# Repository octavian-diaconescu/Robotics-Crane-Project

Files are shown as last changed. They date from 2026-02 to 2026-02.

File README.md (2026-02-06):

# Robotics Crane Project

## Description
The crane can rotate 180° and raise or lower a hook to pick up and place objects anywhere within its operating area. The project prioritizes lightweight construction and simplicity, making it suitable for learning mechanical design, motion control, and basic automation using mostly 3D-printed parts. It is intended as a hands-on platform for experimenting with real-world robotic concepts such as load handling, stability, and coordinated multi-axis movement at a small scale.

## Required Components
- [x] 4 x **Stepper Motors** for controlling each moving part
- [x] 4 x **ULN2003 Motor Drivers**
- [x] **Bluetooth Controller** (e.g., PS4, Xbox, or generic Bluetooth gamepad)
- [x] **ESP32** Board
- [x] 2 x **Breadboard Mini**
- [x] 1 x **Medium Breadboard**
- [x] **Wires/Jumpers** as needed 
- [x] 16 x AA **Alkaline Batteries**
- [x] High tension, low diameter **nylon**(the fishing kind)
- [x] **Lead weights** for creating tension in the hook

## Initial Questions

### 1. What is the system boundary?
The system consists of the crane structure, the ESP32 control board, the breadboard-mounted electronic components (motor drivers), and the motors responsible for rotation, trolley movement, and hook lifting. These components are integrated into the crane assembly, with electronics housed in a 3D-printed enclosure and wiring routed beneath the base platform.

Elements outside the system include the operator, the Bluetooth controller used for wireless input, and the objects being picked up, which interact with the crane but are not part of the control or mechanical system itself.

### 2. Where does intelligence live?
The system's intelligence resides entirely on the ESP32 microcontroller. The Bluetooth controller acts only as a wireless input interface, with all control logic and Bluetooth communication handling executed on the ESP32.

### 3. What is the hardest technical problem?
The primary technical challenge is the mechanical design of the crane, specifically creating reliable rotating and sliding mechanisms using 3D-printed parts that can handle loads without excessive friction or instability. Additionally, implementing stable Bluetooth communication and controller input parsing on the ESP32 presents a secondary challenge.

### 4. What is the minimum demo?
The minimum demo requires the crane to respond to Bluetooth controller input by moving at least one axis and interacting with a real object, such as lifting a small load off the ground. The demo is considered successful if the user can control the motion wirelessly through the Bluetooth controller and observe a clear, repeatable mechanical response.

### 5. Why is this not just a tutorial?
This project goes beyond a tutorial because it requires custom mechanical and control design rather than assembling predefined modules. Decisions about component placement, motion mechanisms, structural constraints, and wireless control implementation must be made and evaluated, making the outcome dependent on design choices instead of following a fixed set of instructions.

## Implementation Details and Challenges

>[!IMPORTANT]
>We decided to have the breadboard next to the crane plate, on the ground level, so we had to run wires up the leg and into the cabin. Due to limited space, the crane can safely operate in a 180 degree range without any of the cables coming loose, and without them getting stuck on the stepper motor responsible for the crane's rotation. This can be fixed by storing the breadboard assembly in the operator cabin, but this would require a much bigger scale.

We have overcome many challenges during the creation of this project. Most were related to creating the 3D models from scratch, using our real-world knowledge to adapt to the constraints of the project. One such constraint was related to size: we wanted to pick a scale that both respects the real-world equivalent, and also keeps the presentation concise and to the point. A crane is fundamental to construction, and while its operation is straightforward, it was very fun and interesting to implement. 



We chose stepper motors in spite of their slow speeds, because we liked their inherent high torque. We consider this to be faithful to real life, as cranes need to lift heavy construction materials at the cost of speed. To power a stepper motor, we need 5V DC, so we connected 4 x AA batteries(in series) per motor, to a total of 16 batteries, each set providing about 6V DC. Two motors control the trolley on the X-Axis, one controls the rotation of the crane on the Z-Axis, and the last controls the hook on the Y-Axis. We wanted the project to look as best it could, so we came up with creative ways to hide the steppers. One is hidden at the back, two are hidden in what would be the crane operator's cabin, and the last is hidden underneath that cabin.



What made this project really challenging was the fact that we didn't settle for schematics available online, but instead modeled the crane ourselves from the ground up. We chose the specific positions of the motors, the movement of the trolley and the size of the _"counter weight"_, using a real crane as an inspiration and adapting things to our needs on the fly. After we figured out how many motors we needed, and their respective uses, we had to come up with creatives ways to incorporate them into a polished 3D body. First, we focused on the trolley functionality: how it would move, how it should look and how it would fit onto the crane's arm. We settled for a horizontal pulley system with a closed loop of nylon(yes, the fishing kind) with two steppers moving it on the X-axis by spinning spools of nylon. This approach isn't perfect, as we lose some of the already low speeds to the low levels of friction between the spools of nylon and the wheels we printed for the steppers. *We couldn't come up with a better way to increase friction between the two without modifying the scale of the project.* At the same time, we designed and printed the arm, which went through about two iterations or so before everything fitted as we wanted it. **Tolerances and plastic warping _are_ real and they _will_ hurt us :c.**



After we decided that the operator cabin would hide most of the components(three drivers and two motors), we had to model it around them and make sure we had enough space to mount everything, all while keeping it proportional to the rest of the crane. Naturally, after printing we realized we omitted a few things, so we had to brute-force it and cut some plastic to make room. Thankfully, the biggest cut was made on the underside of the cabin, so it doesn't affect the project aesthetically. The stepper responsible for the hook is housed at the back of the crane, in the counterweight, and nylon crosses the length of the crane all the way to the front. Another challenge was the hook, as it is too light to keep tension in the string. To overcome this limitation, we used lead spheres, the kind one would use when fishing, to induce more tension in the wire.



The easiest part was writing the code for the motors, as we used a pre-existing library available on GitHub, named [BluePad32](https://github.com/ricardoquesada/bluepad32). This allowed us to easily control the crane assembly with almost any kind of wireless controllers.

We feel like this project, while not being technologically complex, impresses through its aesthetic and solid functionality. It's not perfect, but we had a great deal of fun designing it from the ground up, feeling like true engineers by coming up with creative ideas, adapting on the fly and getting better at it and improving the design through trial and error. As the last blueprint for the Robotics class, this is our _love letter_ and _passion project_.

## How to Control the Crane Assembly
>These controls are viable for both Xbox and Playstation controllers.
crane_project_controlls

## Pin Map

|Motor|ULN2003 Pins|ESP32 GIOP Pins|
|-----|---|---|
|Motor 1|IN1, IN2, IN3, IN4|25, 26, 27, 14|
|Motor 2|IN1, IN2, IN3, IN4|32, 33, 22, 23|
|Motor 3|IN1, IN2, IN3, IN4|18, 19, 21, 4|
|Motor 4|IN1, IN2, IN3, IN4|16, 17, 5, 13|

 

## Pictures and Demo
 [Youtube Link](https://youtu.be/Kfjp9-Fd0ek)
<details>
  <Summary>
  Pictures  
  </Summary>
  
  
  
  
  
  
</details>



## Credits
>[!NOTE]
>This project took roughly 15 hours to model, 30 hours to print and 16 hours to assemble and test.

This project will be made in collaboration with [octavian-diaconescu](https://github.com/octavian-diaconescu) and [Sed4u](https://github.com/Sed4u).

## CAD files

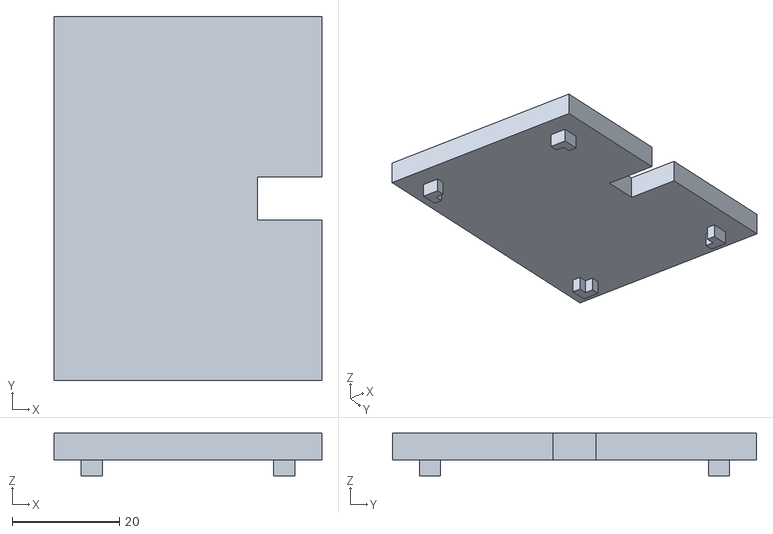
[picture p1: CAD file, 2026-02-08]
STLs/CounterWeightLid.stl
50.0 x 68.0 x 8.00

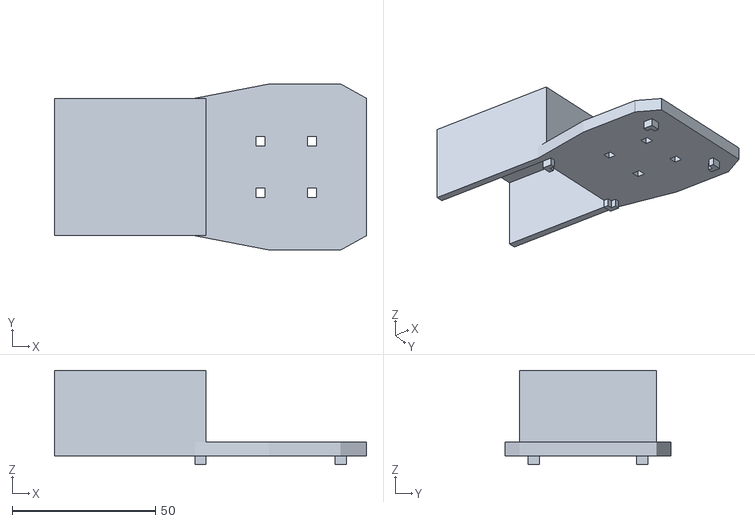
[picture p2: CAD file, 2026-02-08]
STLs/OperatorCabinLid.stl
109.0 x 58.0 x 33.0

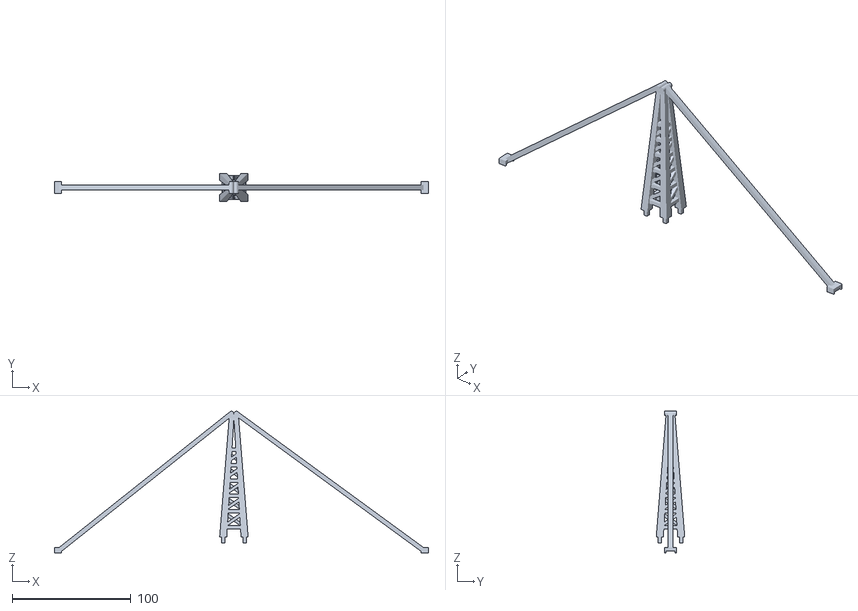
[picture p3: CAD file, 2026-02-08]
STLs/UpperCraneDecorativeParts.stl
315.0 x 24.0 x 119.3

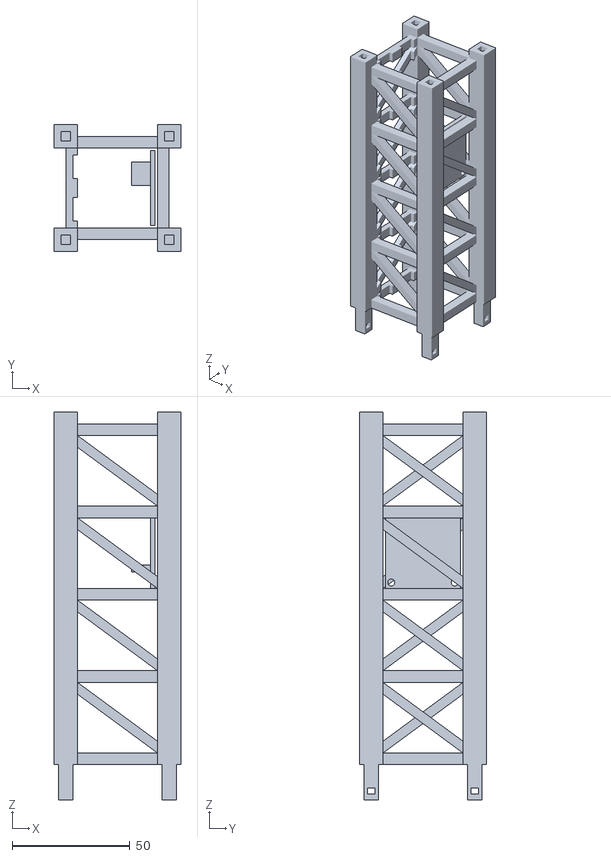
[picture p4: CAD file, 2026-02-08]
STLs/LowerPartOfCraneTower.stl
54.0 x 54.0 x 165.0

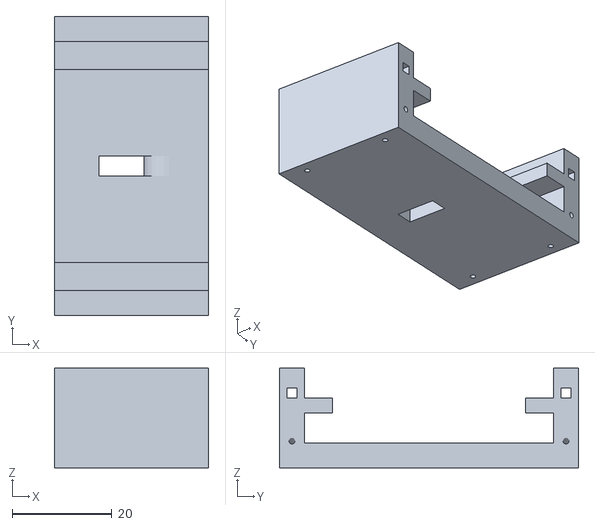
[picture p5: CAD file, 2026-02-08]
STLs/Trolley.stl
31.0 x 60.0 x 20.0

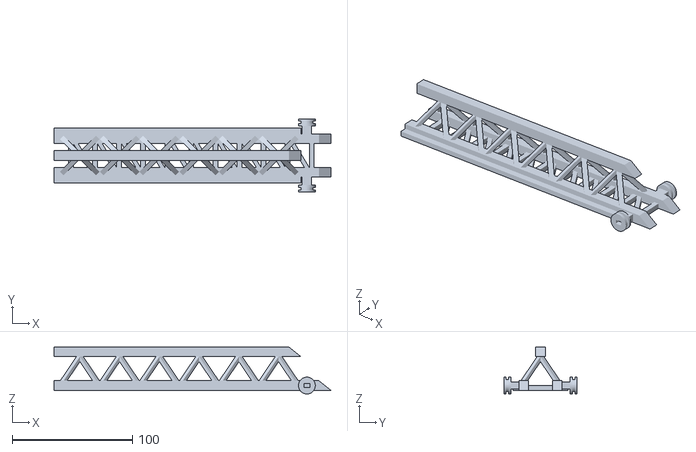
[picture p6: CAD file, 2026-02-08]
STLs/Jib.stl
230.0 x 61.0 x 39.0

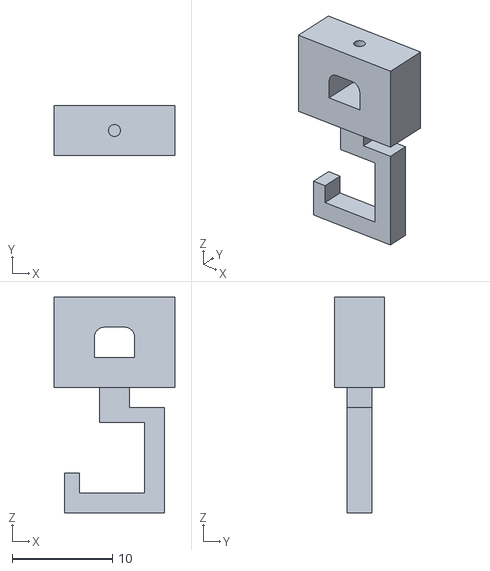
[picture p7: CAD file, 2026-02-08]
STLs/Hook.stl
12.0 x 5.00 x 21.5

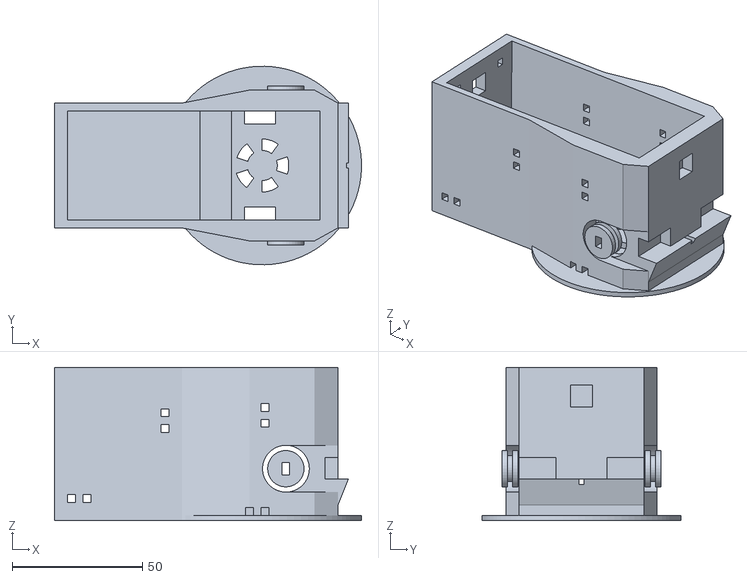
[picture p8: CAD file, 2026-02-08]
STLs/OperatorCabin.stl
118.1 x 76.3 x 59.0

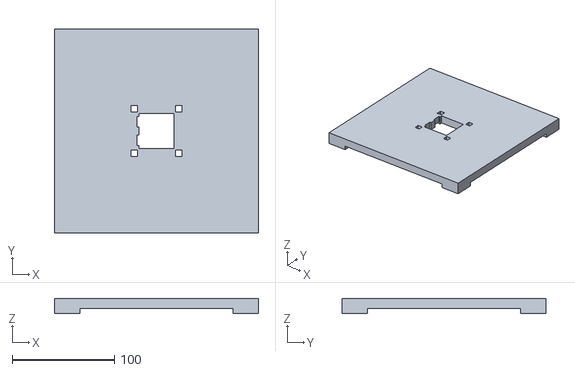
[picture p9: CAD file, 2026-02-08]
STLs/CranePlate.stl
200.0 x 200.0 x 15.0

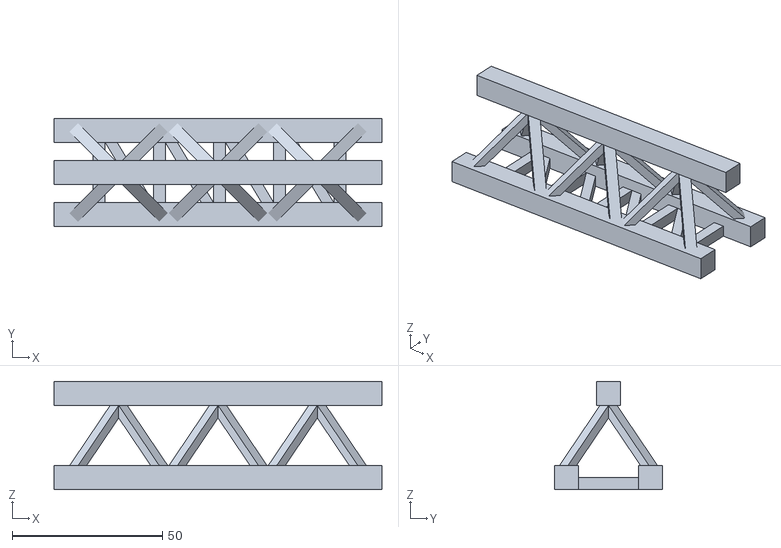
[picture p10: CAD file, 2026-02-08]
STLs/BackJib.stl
109.0 x 36.0 x 36.0

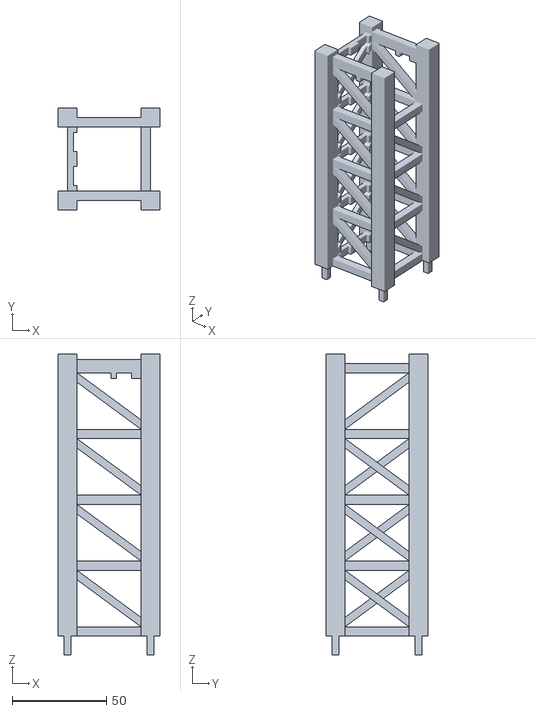
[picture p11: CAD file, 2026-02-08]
STLs/UpperPartOfCraneTower.stl
54.0 x 54.0 x 160.0

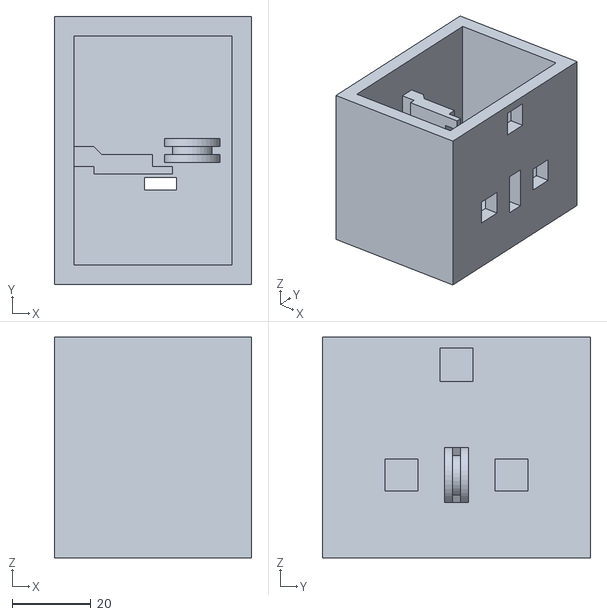
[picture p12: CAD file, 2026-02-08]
STLs/CounterWeight.stl
50.0 x 68.0 x 56.0

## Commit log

2026-01-16 Updated Project Implemetation
    Opted for a wireless bluetooth control system via the ESP32 board instead of joysticks wired to Arduino
2026-02-08 Added crane STLs
    [BackJib.stl, CounterWeight.stl, CounterWeightLid.stl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]
